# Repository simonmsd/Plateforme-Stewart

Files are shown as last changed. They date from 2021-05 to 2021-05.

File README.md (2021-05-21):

# Plateforme-Stewart
Réalisation d'une plateforme de stewart et  du tableur pour la contrôler.

Le document "Rapport_Projet.pdf" vous permet de découvrir notre travail et d'obtenir des informations sur comment nous avons réalisé le tableur et la plateforme.

Le document "Tableur_Stewart.xlsx" vous permet de déterminer les longueurs à donner aux bielles reliant les deux plateaux. Pour ce faire, il faut initialiser les paramètres des la plateforme dans les cellules "B1" à "B4". Ensuite, il faut entrer la position cible de la plateforme dans la colonne nommée "Cible" qui est la colonne "X", utiliser la fonction solveur d'Excel et lire les longueurs à donner aux bielles dans la colonne nommée "Longueurs ajustées" qui est la colonne "R".    

Dans le document "Vidéo de démonstration", vous trouverez un lien permettant d'accéder à une vidéo du foctionnement du tableur et de la plateforme de Stewart.

Le document "Rapport Projet.tex" est le code Latex qui a permis de créer le document pdf.

Dans le dossier "modélisations", vous trouverez les modélisations des deux plateaux de la plateforme de Stewart. Ces modélisations ont été réalisées avec le logiciel FreeCAD.

Dans le dossier "images", vous trouverez toutes les illustrations inclues dans le rapport du projet.

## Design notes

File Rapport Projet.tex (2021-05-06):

\documentclass[a4paper,12pt]{article}

% passe en mode large sur la page A4
\usepackage{a4wide}

% document francisé
\usepackage[french]{babel}

% permet la frappe de caractères accentués
\usepackage[utf8x]{inputenc}

\usepackage{bookmark}
\usepackage[T1]{fontenc}
\usepackage{color}
\usepackage{amsmath}
\usepackage{amsfonts}
\usepackage[top=3cm, bottom=3cm, left=2.5cm, right=2.5cm]{geometry}
\usepackage{fancyhdr}
\usepackage{graphicx}
\usepackage{float}
\usepackage{multicol}
\usepackage{multirow}
\usepackage{textcomp}
\usepackage{gensymb}
\usepackage{subcaption}
\usepackage{url}
\usepackage{hyperref}
\usepackage[justification=centering]{caption}

\pagestyle{fancy}

\makeatletter
\newcounter{subsubsubsection}[subsubsection]
\renewcommand\thesubsubsubsection{\@roman\c@subsubsubsection}
\newcommand\subsubsubsection{\@startsection{subsubsubsection}{4}{\z@}%
                                     {-3.25ex\@plus -1ex \@minus -.2ex}%
                                     {1.5ex \@plus .2ex}%
                                     {\normalfont\small\bfseries}}
\newcommand*\l@subsubsubsection{\@dottedtocline{3}{5.2em}{1em}}
\newcommand*{\subsubsubsectionmark}[1]{}
\setcounter{secnumdepth}{4}
\makeatother

% individualisation des paramètres de la page
%\parskip7pt
\setlength{\topmargin}{-10mm}
%\setlength{\textheight}{250mm}

%En-tête
\renewcommand{\headrulewidth}{0.3pt}
\fancyhead[C]{}
\fancyhead[L]{L1 CMI OPT/IM -- ICM -- INA}
\fancyhead[R]{Projet d'initiation à l'ingénierie}
\setlength{\headheight}{15pt}
%Pied de page
\renewcommand{\footrulewidth}{0.3pt}
\fancyfoot[L]{2020-2021}
\fancyfoot[C]{\textbf\small{\thepage}}
\fancyfoot[R]{\footnotesize{Rapport final}}

\begin{document}

%
% -------------------------------------------------------------------------------------------
%
\begin{figure}[H]
  \centering
  
\end{figure}

\begin{center}
	{\large {L1 CMI -- Projet d'initiation à l'ingénierie}} \\
	\vspace{6cm}
  {\Large \textbf{Conception et réalisation de la plateforme de Stewart} \\
	\vspace{2mm}
	Etudiants : Baptiste Deshayes, Malo Le Bourlout, Simon Massonnaud, Eliott Petiteau

    Encadrants : Rabah Bouzidi et  Nicolas Dupont-Bloch\\
	\vspace{9cm}	
	Janvier - mai 2021} \\
	\vspace{3mm}
	
\end{center}

\newpage

\tableofcontents

\newpage
%
% ====================================================================
%
\section{Introduction}

La plateforme de Stewart est un positionneur hexapode composé d’un plateau fixe et d’un plateau mobile. 
Ces deux plateaux sont maintenus à l’aide de six actionneurs linéaires qui s’apparentent à des vérins \textit{(nous les nommerons indifféremment aussi dans le rapport bielles ou tendeurs)}. Le but de cette plateforme est de s'adapter à tous les mouvements possibles.
Le plateau supérieur peut se déplacer selon les trois axes (x, y et z), il peut également s’incliner suivant trois axes. 
Grâce à ces six bielles pouvant indépendamment changer de longueur, la plateforme supérieure peut former n’importe quel plan, elle est juste limitée par la longueur des bielles. 
Il faut actionner les six bielles qui relient les deux plateaux pour faire varier leur longueur et ainsi changer l’orientation de la plateforme. 
Chaque position de la plateforme supérieure correspond à une seule combinaison des six longueurs.

\begin{figure}[H]
  \centering
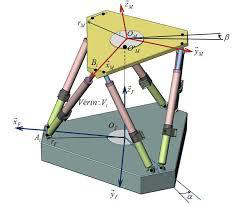
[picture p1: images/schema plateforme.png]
  
  \caption{Illustration de la plateforme de Stewart}
\end{figure}

\medskip

Cette plateforme peut avoir de nombreux usages. 
Elle peut être utilisée comme base pour une cabine de simulateur de vols, pour la conception de grues, la recherche
sous-marine ou encore pour les télescopes. 
Effectivement, la nature de ces activités nécessite un positionnement très précis et la plateforme de
Stewart répond à ce besoin. 
D’un coté, cette plateforme est une avancée technologique dans de nombreux secteurs car elle joue le rôle de simulateur. Elle permet donc d’anticiper des comportements sans avoir à réaliser des
tests en conditions réelles. Et d’un autre coté, cette plateforme a permis une excellente précision par rapport à ce qu'il était possible de réaliser auparavant.

\medskip

Notre projet a pour but d’équiper un télescope de Newton. 
Le principe de ce télescope est assez simple, en forme de tube. 
Les rayons lumineux rentrent à une extrémité du tube et sont projetés sur un miroir concave afin de diriger les rayons vers un autre miroir en face du premier. 
C’est ce deuxième miroir que nous regardons avec notre oeil sur le coté du tube ; ce miroir est incliné afin de changer la direction des rayons lumineux et de les faire parvenir à notre oeil. 
Pour avoir l’image la plus nette possible, il faut limiter le nombre de miroirs. 
Nous pouvons donc imaginer un télescope ayant juste le premier miroir et mettre notre oeil en face de ce dernier afin d’avoir une image la plus nette possible. 
Le problème est que notre tête va créer un zone d’obstruction trop importante. 
En effet, notre tête va éclipser une partie du ciel que nous voulons observer. 
Le but est donc de réduire au maximum cette zone d’obstruction. 
On utilise pour cela une caméra car elle est bien moins volumineuse que notre tête. 
On l’utilise également pour capter ces images et en prendre un cliché. 
Cette caméra nécessite d’être fixée au télescope et d’être à bonne distance du miroir. 
Il faut que la caméra soit à bonne distance afin d’être exactement sur le point focal, c’est la distance à laquelle tous les rayons réfléchis par le miroir concave se rejoignent et forment une image nette. 
Pour s’assurer que la caméra soit à la bonne distance, nous allons utiliser la plateforme de Stewart. 
Nous fixerons la caméra au centre du plateau supérieur et le plateau bas sera relié au télescope. 
Nous pourrons alors ajuster la position de la caméra très précisément afin d’être à la bonne distance focale. 

\begin{figure}[H]
    \centering
    \begin{subfigure}[]{0.4\textwidth}
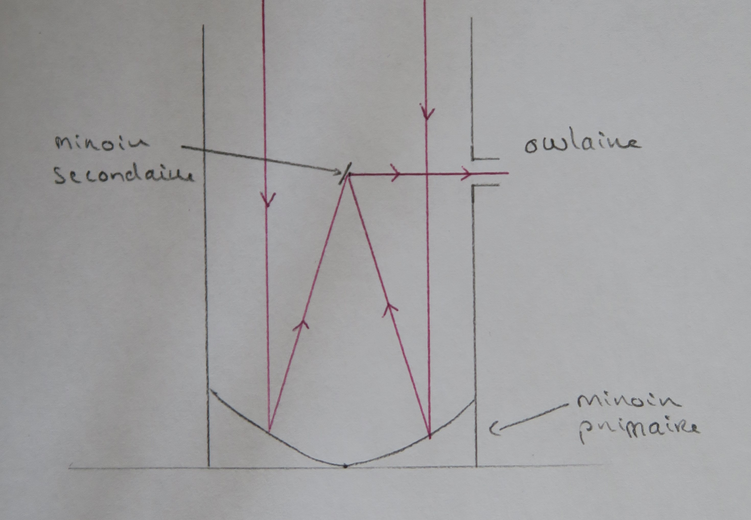
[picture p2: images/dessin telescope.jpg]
        
    \end{subfigure}
    \begin{subfigure}[]{0.4\textwidth}
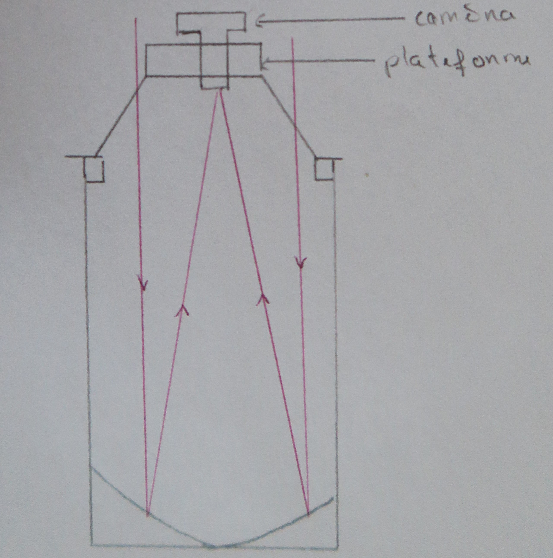
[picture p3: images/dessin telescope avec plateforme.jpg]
        
    \end{subfigure}
    \caption{Schéma du télescope de Newton avec et sans la plateforme de Stewart}
\end{figure}

\medskip

La temporalité du projet s'est séquencée en cinq temps : \\
-échanges/discussions avec notre encadrant sur les créneaux de cours pour guider l'avancement de notre projet ; \\
-échanges/discussions entre nous quatre pour mettre en commun et confronter nos temps de travail individuel, décider des options de conception et modélisation à prendre et de la marche à suivre pour engager les différentes étapes du projet ; \\
-temps de regroupement pour mettre en application ( = montage de la plateforme) ; \\
-finalisation de la réalisation de la plateforme ( = ajustements du montage) durant les vacances de printemps ; \\
-co-rédaction du rapport final.

\newpage

\section{Problématique}

Le problème traité dans ce projet est la réalisation d'une plateforme de Stewart qui se décompose en quatre étapes : \\
- la conception de celle-ci, en accord avec les dimensions requises pour sa future utilisation (ajuster la position d'une caméra sur un télescope de Newton), à l'aide d'un logiciel de modélisation 3D (ici FreeCAD) ; \\
- la création d'un tableur permettant de calculer et d'optimiser les longueurs des actionneurs linaires en fonction de la position voulue de la plateforme ; \\
- l'impression en 3D des pièces modélisées, l'achat des pièces de jonction et des actionneurs linéaires ; \\
- et enfin l'assemblage de la plateforme.

\medskip

Afin de créer une plateforme de Stewart, il nous est nécessaire de connaître  la cinématique de la plateforme et comment elle est affectée par les variations de longueur des six éléments linéaires qui la composent.
Il nous faut donc établir les différentes équations permettant de retrouver la longueur de chacun des éléments linéaires en fonction des mouvements de translation et de rotation que nous souhaitons effectuer. 

\medskip

La plateforme de Stewart est un outil dont l'utilisation est déjà répandue dans de multiples domaines, possédant donc diverses analyses sur son comportement, souvent abordées par cinématique inversée. 
Ses applications en robotique ont notamment fourni des analyses d'un point de vue électronique de la plateforme, ainsi que de sensibilité de ses mouvements dans le cadre de différents usages tel l'aéronautique.

\newpage

\section{Mise en oeuvre de la plateforme}

Dans cette partie, nous allons voir comment résoudre le problème posé. 
Cette résolution passe par deux grandes étapes.
Dans un premier temps, nous devons réaliser le modèle mathématique qui permet de contrôler la plateforme, nous avons pour cela créé un tableur Excel. Dans un second temps, nous devons créer la plateforme en elle-même, c'est-à-dire la modéliser pour qu'elle réponde à toutes les contraintes amenées par et pour sa future utilisation.

\subsection{Formulation cinématique}
	
L’objectif de ce tableur est de créer un modèle mathématique théorique et précis pour contrôler le fonctionnement de la plateforme de Stewart. 
Nous supposons, pour créer ce modèle, que la plateforme s’apparente à deux disques reliés par six axes et espacés d’une hauteur fixée quand l’appareil est au repos. 
Nous avons séparé notre travail en étudiant d’un côté, la partie basse de la plateforme et de l’autre, sa partie haute.

\subsubsection{Partie basse de la plateforme}

Intéressons-nous à la partie basse. 
Nous supposons que le disque qui la constitue est divisé en trois. C’est-à-dire que chaque point est séparé de cent vingt degrés en prenant des points aux angles 0\degree, 120\degree et 240\degree. 
Ensuite, nous fixons un écart par rapport à ces angles qui peut être choisi par l’utilisateur. 
Nous appelons cet écart \og delta thêta \fg. Il représente la position des six points d’accroches de nos axes. 
De chaque côté des trois angles principaux, de 0\degree, 120\degree et 240\degree, nous ajoutons la valeur de \og delta thêta \fg \ pour trouver un premier point et nous la retirons pour trouver un deuxième point. 
Prenons un exemple pour illustrer le fonctionnement de ce \og delta thêta \fg . 
Prenons-le de 30\degree et prenons le point à l’angle 0\degree. Comme expliqué, nous trouvons donc un point à 30\degree et un autre à -30\degree ou 330\degree. 
Une fois ces points déterminés, nous calculons leur valeur en radians. 
De ces valeurs en radians, nous pouvons déterminer les coordonnées des points selon les axes x, y et z. 
Pour la coordonnée selon l’axe z, elle vaut 0 car nous sommes sur la partie basse de la plateforme. 
Pour les coordonnées selon les axes x et y, nous appliquons respectivement la fonction cosinus et sinus à chaque angle tout en multipliant par le rayon de la plateforme. 
Nous connaissons donc les coordonnées des six points bas de la plateforme.

\begin{figure}[H]
  \centering
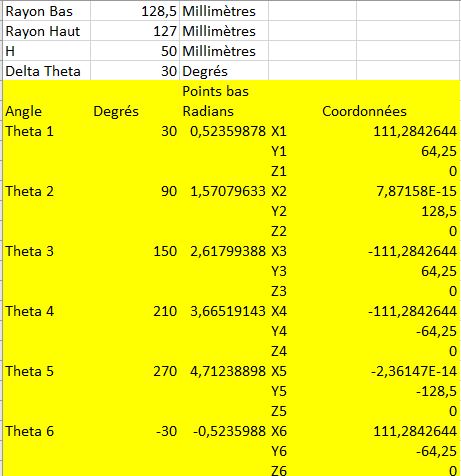
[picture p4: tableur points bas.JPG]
  
  \caption{Tableur points bas}
\end{figure}

\subsubsection{Partie haute de la plateforme}

Intéressons-nous maintenant à la partie haute de la plateforme. 
Nous supposons que ce disque est parfaitement parallèle à la partie basse et que ces deux disques sont séparés d’une hauteur fixée nommée \og h \fg . 
Nous supposons là aussi que le disque est séparé en trois points selon les mêmes positions que pour la partie basse de la plateforme. 
Ces trois points représentent les points d’arrivées des six axes qui partent de la partie basse. 
Nous calculons, suivant le même raisonnement que précédemment, les coordonnées de ces points selon les axes x, y et z, à une différence près. 
En effet, comme nous étudions maintenant la partie haute de la plateforme, nous nous trouvons à une hauteur \og h \fg \ de la partie basse. 
Ainsi la coordonnée selon l’axe z vaut h.  
Nous connaissons maintenant les coordonnées théoriques de chacun des trois points de la partie haute de la plateforme. 
Ces coordonnées théoriques seront modifiées par la suite lors de l’utilisation de la plateforme. 
Ces nouvelles coordonnées seront appelées \og coordonnées ajustées \fg . 
Au début, nous initialisons ces coordonnées ajustées avec les coordonnées théoriques pour continuer de réaliser le modèle mathématique.  
Nous calculons ensuite les écarts entre les points AB, AC et BC selon les axes x, y et z. 
Pour cela, nous calculons la différence entre les coordonnées. 
Ensuite, à partir de ces distances entre tous les points, nous pouvons calculer la norme des trois vecteurs que sont $\overrightarrow{AB}$, $\overrightarrow{AC}$, et $\overrightarrow{BC}$. Nous définissons également une valeur cible pour la norme des vecteurs. 
Cette valeur vaut racine de trois multipliée par le rayon de la plateforme haute. 

\begin{figure}[H]
  \centering
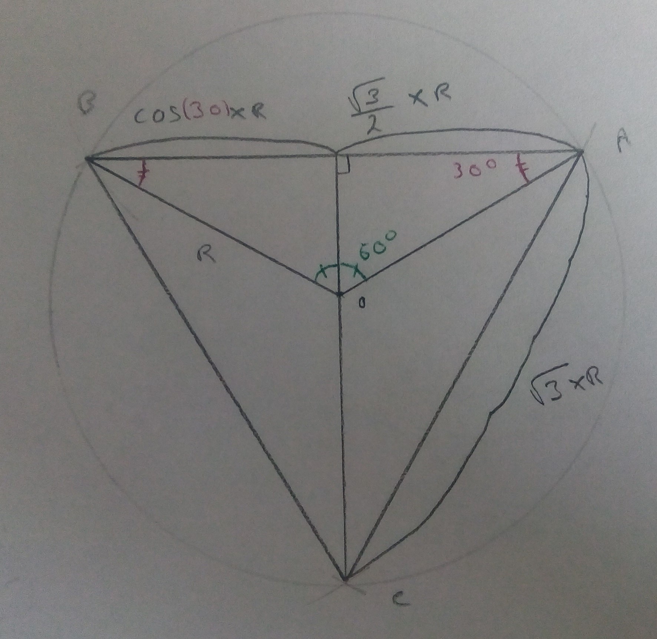
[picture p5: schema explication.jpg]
  
  \caption{Schéma d'explication pour le calcul de la norme des vecteurs}
\end{figure}

Nous calculons ensuite le produit vectoriel de $\overrightarrow{AB}$ par $\overrightarrow{AC}$ ainsi que sa norme car ce calcul va intervenir plus tard dans le tableur. 
Nous créons également une colonne qui contiendra les coordonnées ajustées des points hauts, mais nous y reviendrons plus tard. En effet, cette colonne n'intervient qu'à la toute fin du tableur.

\begin{figure}[H]
  \centering
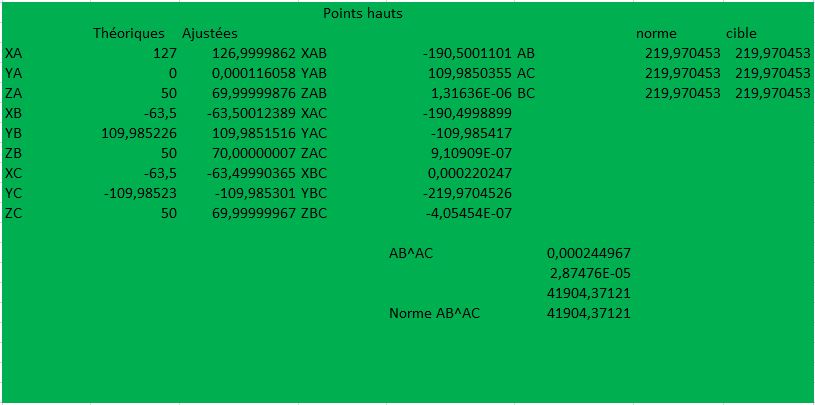
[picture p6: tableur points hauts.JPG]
  
  \caption{Tableur points hauts}
\end{figure}

\subsubsection{Longueurs des bielles qui relient les plateaux}

Maintenant que nous connaissons les coordonnées de tous les points d'accroches, nous pouvons raisonner sur la longueur des bielles, ce qui est l'objectif principal, c'est-à-dire déterminer leurs longueurs en fonction de la position voulue. 
Pour chacune des bielles, nous calculons sa longueur à partir des coordonnées théoriques de chaque point. 
Nous calculons la différence entre la coordonnée du point haut et celle du point bas selon chaque axe. 
Nous élevons ces différences au carré puis nous ajoutons les valeurs pour chaque axe et nous en prenons la racine carrée afin de connaître la longueur de la bielle. 
Étant donné que nous avons six bielles, nous répétons l'opération pour chacune d'elles. 
Dans cette partie du tableur, nous créons une colonne appelée \og longueurs ajustées \fg . 
C'est dans celle-ci que nous pourrons lire la valeur de la longueur qu'il faudra donner à chaque bielle pour pouvoir placer la plateforme à la position voulue. 
Nous créons, pour clôturer cette partie du tableur, une dernière colonne dans laquelle nous pouvons lire l'écart de longueur delta entre les bielles à l'origine et la longueur de chaque bielle pour la position voulue.

\begin{figure}[H]
  \centering
  
  \caption{Tableur bielles}
\end{figure}

\subsubsection{Valeurs cibles à obtenir}

Voyons maintenant la dernière partie du modèle mathématique, celle qui nous permet de donner la position souhaitée de la plateforme et qui permet de déterminer la longueur à donner aux bielles. Pour commencer, nous déterminons la position du point au centre du plateau haut. 
Nous appelons ce point \og G \fg. 
La coordonnée en x de ce point est la moyenne des coordonnées ajustées des points hauts selon cet axe. 
Nous suivons la même procédure pour chacun des axes. 
Nous créons ensuite une partie dédiée au centre de masse de la plateforme haute. 
Pour déterminer la valeur selon x de ce centre de masse, nous effectuons simplement la division de la coordonnée en x du produit vectoriel de $\overrightarrow{AB}$ par $\overrightarrow{AC}$ par sa norme. 
Nous répétons le même calcul pour les deux autres axes. 
Ensuite, nous créons une colonne où nous entrons les valeurs \og cibles \fg. 
Ces valeurs correspondent à la position que nous voulons donner au point qui est au centre de la plateforme, le point G. 
Nous pouvons également donner une valeur cible aux coordonnées en x et y du centre de masse. Ensuite, nous calculons les écarts entre la valeur cible et la valeur théorique des coordonnées du point G et du centre de masse. 
Nous élevons ces écarts au carré pour n'avoir que des valeurs positives. 
Nous sommons ensuite tous ces écarts, ce sera notre fonction \og coût \fg. 
Nous faisons également le choix de pouvoir donner des coefficients à ces valeurs pour agir plus ou moins sur le centre de masse ou les coordonnées du point G.

\begin{figure}[H]
  \centering
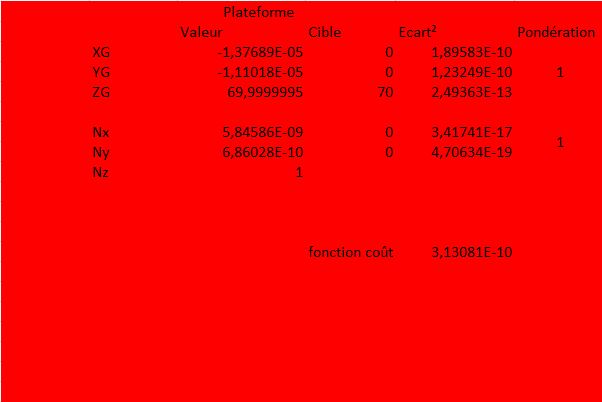
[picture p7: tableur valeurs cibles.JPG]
  
  \caption{Tableur valeurs cibles}
\end{figure}

\subsubsection{Fonction solveur}

Maintenant nous allons expliquer comment nous obtenons les longueurs ajustées des bielles. 
Nous utilisons pour cela la fonction solveur du tableur Excel. 
Le but est de minimiser la fonction coût, qu'elle soit la plus proche possible de zéro. 
Nous avons également une contrainte : il faut que les normes des vecteurs $\overrightarrow{AB}$, $\overrightarrow{AC}$, et $\overrightarrow{BC}$ soient égales ou du moins les plus proches possibles des normes cibles de ces vecteurs. 
Nos variables sont les coordonnées ajustées des points hauts. 
En les modifiant, nous calculons les longueurs ajustées des bielles qui sont donc les longueurs finales à donner aux bielles pour avoir la plateforme à la position souhaitée. 
En appliquant donc la fonction solveur, nous pouvons pour chaque position souhaitée obtenir la longueur à donner aux bielles.

\begin{figure}[H]
  \centering
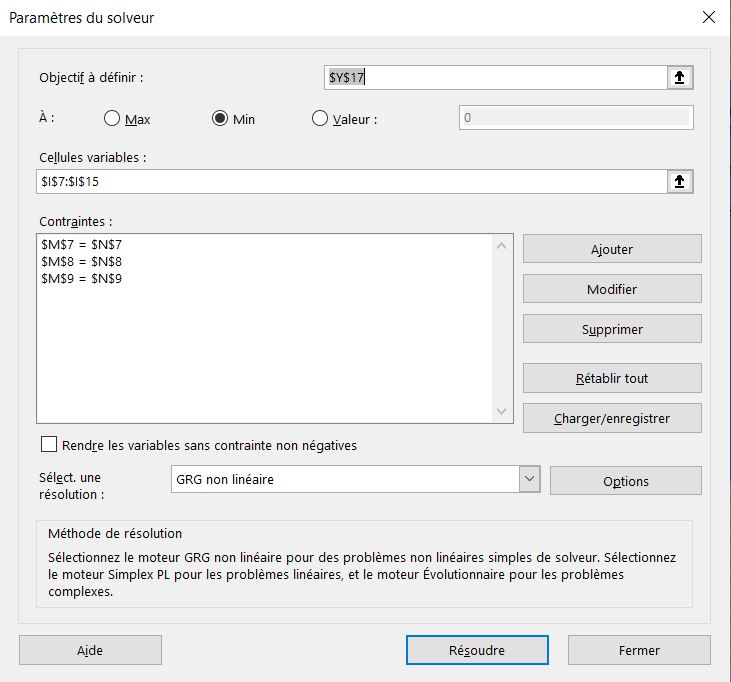
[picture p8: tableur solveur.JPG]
  
  \caption{Tableur solveur}
\end{figure}

\subsection{Réalisation de la plateforme}
La plateforme est composée de deux plateaux, un plateau inférieur et un plateau supérieur. 
Les attentes de ces deux plateaux sont différentes donc leur apparence et leur modélisation le seront aussi.

\subsubsection{Contraintes de la plateforme}

\subsubsubsection{Plateau inférieur}

Le plateau inférieur a quelques contraintes,
notamment cette première : obstruer le moins possible le passage de la lumière qui doit arriver jusqu’au télescope. 
Pour cela nous décidons de l'évider (ne modéliser que les bords extérieurs du cercle). 
Le plateau doit aussi s’emboîter parfaitement dans le tube du télescope sans bouger et ainsi garder l’ensemble de la plateforme stable. 
Nous décidons donc de créer une bordure de quelques millimètres, ainsi une partie s’imbriquera parfaitement dans le télescope et l’autre sera trop grande empêchant la plateforme de rentrer entièrement. 
Enfin, nous devons modéliser six trous à intervalles réguliers qui faciliteront le perçage après impression, intervalles choisis au préalable via les calculs mathématiques précédemment exposés et selon les besoins de la plateforme. 
Ces trous serviront plus tard à visser les tendeurs, il faut donc les modéliser en gardant bien cette idée à l’esprit. C’est pourquoi nous les modélisons sur la plus grande bordure (extérieure au tube du télescope) pour éviter une quelconque gêne des tendeurs à la pose ou à la stabilité de la plateforme dans le tube.

\begin{figure}[H]
  \centering
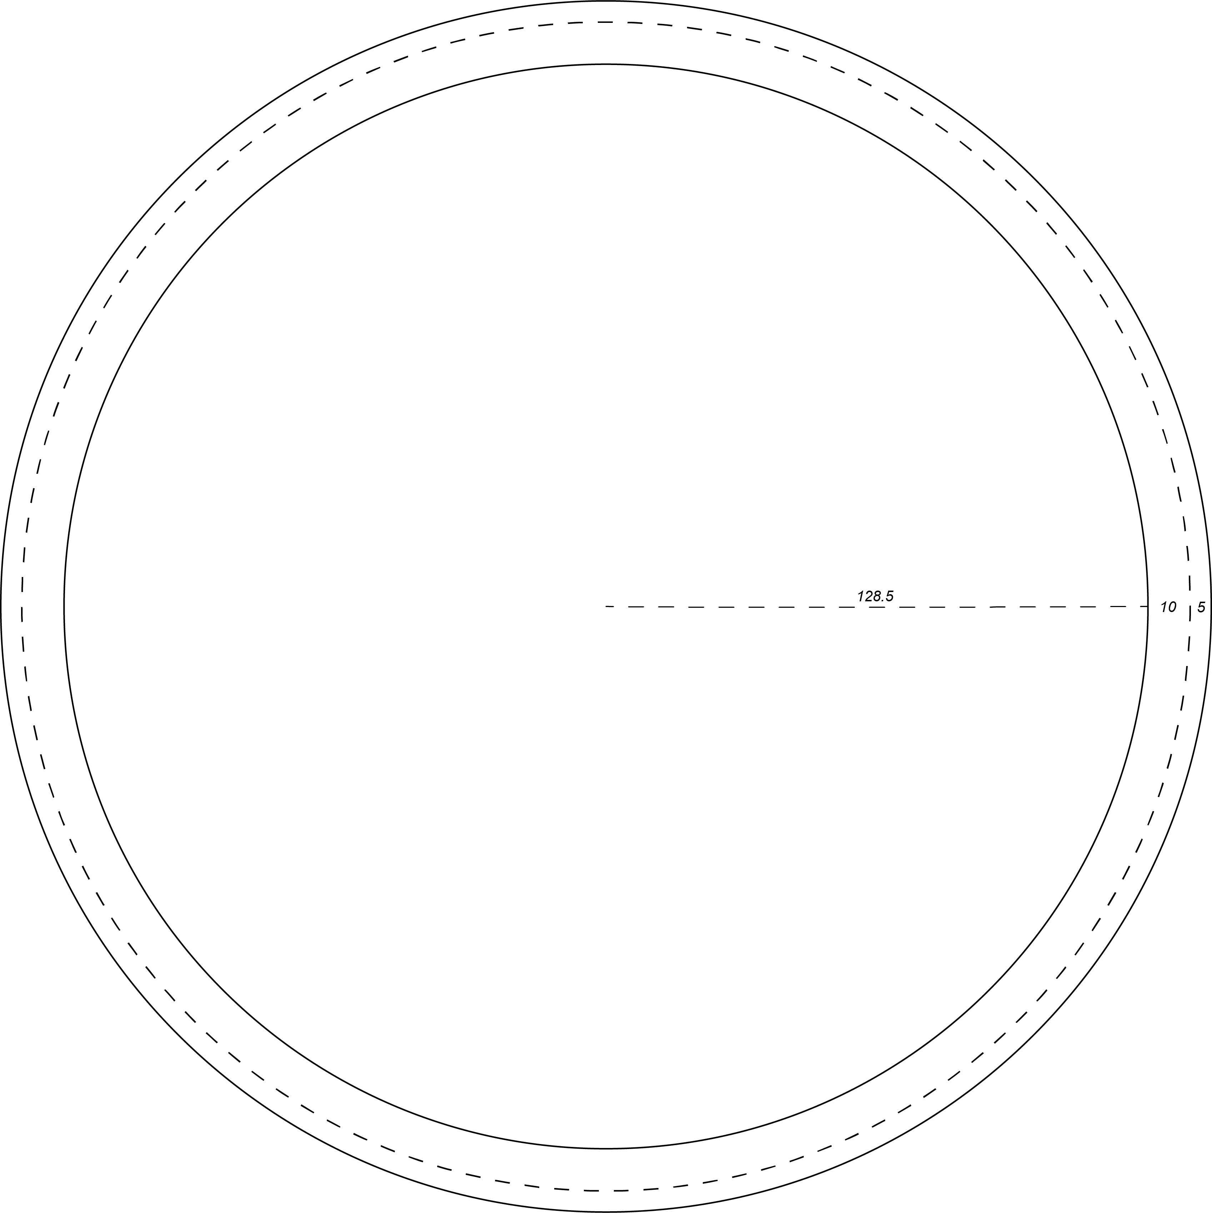
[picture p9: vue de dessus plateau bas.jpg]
  
  \caption{Vue de dessus plateau bas}
\end{figure}
\begin{figure}[H]
  \centering
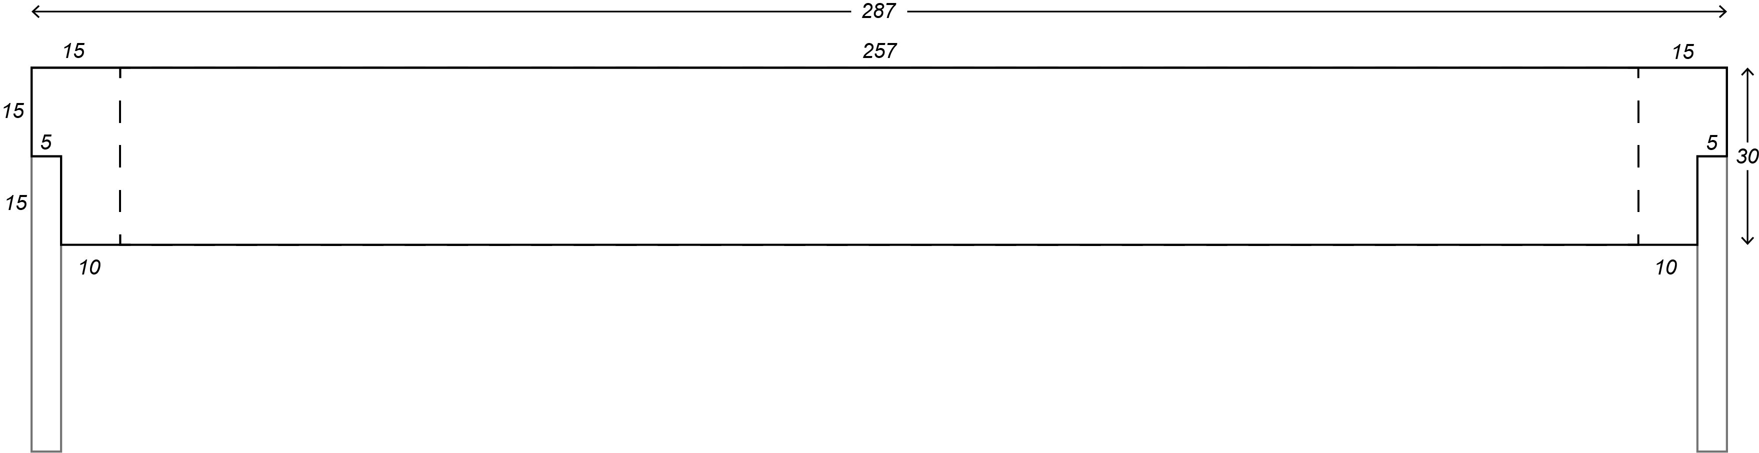
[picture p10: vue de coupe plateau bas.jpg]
  
  \caption{Vue de coupe plateau bas}
\end{figure}

\subsubsubsection{Plateau supérieur}

Pour le plateau supérieur, la première contrainte est la même : obstruer le moins possible le passage de la lumière.
Mais sachant que ce plateau doit porter en son centre une caméra, la tâche est plus compliquée que précédemment ; nous y reviendrons point par point.
Comme le plateau doit porter une caméra, il doit être en conséquence assez résistant, donc plus large.
Nous ne modélisons donc, sur le même principe que le plateau inférieur, que les bords extérieurs et laissons le centre évidé pour laisser passer la lumière.  
Il doit aussi contenir de la matière au centre  pour poser la caméra. Nous modélisons donc un rond central évidé où emboîter la caméra. 
La question d’obstruction de la lumière ne vient pas ici car la caméra étant posée dessus, elle obstruerait de toute façon la lumière.
Il nous faut maintenant relier le cercle central aux bordures car seulement les bordures seront portées par les tendeurs, nous le rappelons. 
Il faut modéliser des branches reliant les différentes parties du plateau. Mais pas trop en nombre ni trop larges pour ne pas obstruer la lumière. 
Nous modélisons donc trois branches, nombre raisonnable choisi arbitrairement, mais facilitant la modélisation par rapport aux six trous sur le plateau qui seront groupés par deux. 
Pour augmenter la résistance des branches sans obstruer davantage la lumière, nous les modélisons avec plus de matière dans le sens de la hauteur.
Mais si toute la plateforme est faite ainsi, il y aura un problème pour l’accès des tendeurs entre les deux plateformes avec le surplus de matière les empêchant de bouger sans contrainte. 
Nous enlevons donc de la matière petit à petit à partir du centre, laissant ainsi une partie volumineuse et solide au niveau de la caméra et une partie plus fine en extérieur laissant plus libre champ aux tendeurs.

\begin{figure}[H]
  \centering
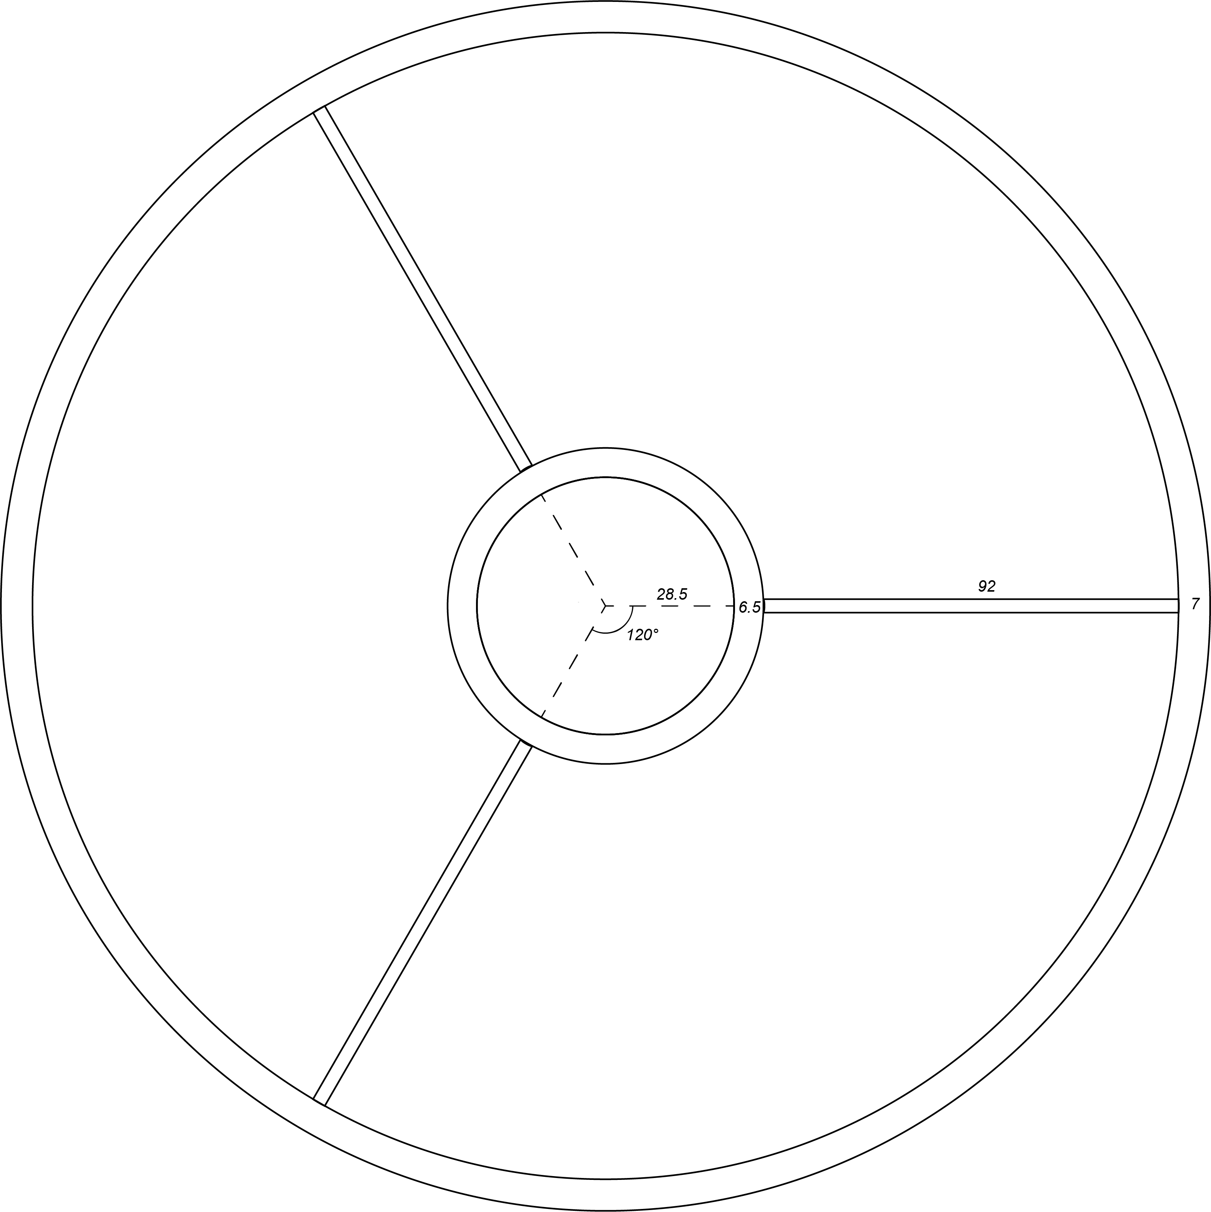
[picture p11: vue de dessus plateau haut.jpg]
  
  \caption{Vue de dessus plateau haut}
\end{figure}

\begin{figure}[H]
  \centering
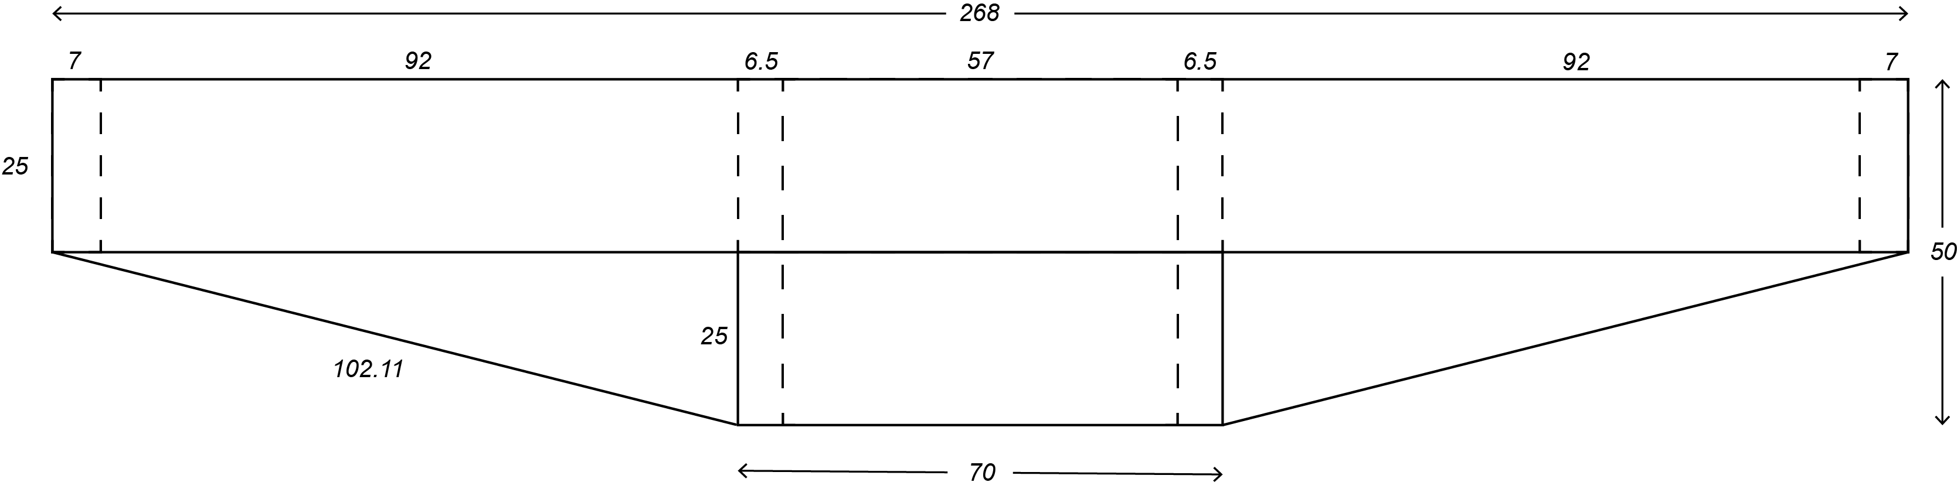
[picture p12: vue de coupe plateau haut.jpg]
  
  \caption{Vue de coupe plateau haut}
\end{figure}

\subsubsection{Modélisation de la plateforme}

\subsubsubsection{Plateau inférieur}

Modélisation du plateau inférieur :
modélisation avec le logiciel FreeCAD. Fonctionnement à partir de schéma 2D auquel nous rajoutons de la matière. Nous réalisons donc d’abord sur le schéma deux cercles différents avec les diamètres  aux bordures afin d’y ajouter plus ou moins de matière et créer la bordure nécessaire.

\begin{figure}[H]
    \centering
    \begin{subfigure}[]{0.4\textwidth}
        
    \end{subfigure}
    \begin{subfigure}[]{0.4\textwidth}
        
    \end{subfigure}
    \caption{Schéma et modélisation du plateau bas}
\end{figure}

Pour finir, il nous faut modéliser des petits trous afin de faciliter le perçage après impression.
Pour enlever la matière, même principe que pour en créer : d’abord, faire un schéma 2D du trou recherché puis enlever la matière en fonction de ce schéma. 
Pour éviter de faire six schémas pour chacun des six trous, il existe une fonctionnalité sur FreeCAD qui répète une action de façon circulaire. Donc, une fois le premier trou modélisé, il suffit de rentrer le nombre de trous souhaités et ils sont repartis de façon régulière autour de l’axe choisi.

\begin{figure}[H]
    \centering
    \begin{subfigure}[]{0.4\textwidth}
        
    \end{subfigure}
    \begin{subfigure}[]{0.4\textwidth}
        
    \end{subfigure}
    \caption{Schéma et modélisation des trous du plateau bas}
\end{figure}

\subsubsubsection{Plateau supérieur}

Même principe pour le plateau supérieur. D’abord, effectuer le schéma avant d’ajouter ou de retirer la matière.
Nous commençons donc par dessiner et modéliser juste une partie du plateau pour une question de précision lors du placement des branches. Puis, nous modélisons les trous au bout de la branche présente à l’aide toujours de schéma.

\begin{figure}[H]
    \centering
    \begin{subfigure}[]{0.25\textwidth}
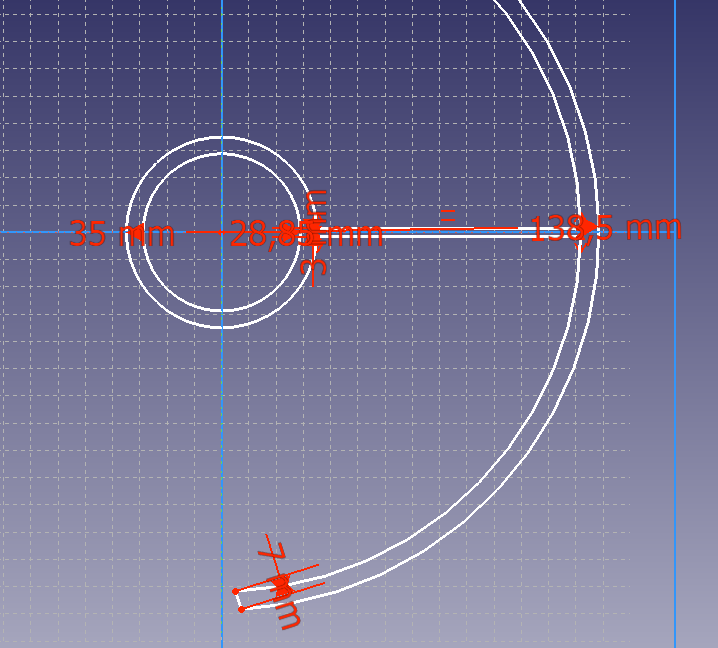
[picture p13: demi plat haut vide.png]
        
    \end{subfigure}
    \begin{subfigure}[]{0.3\textwidth}
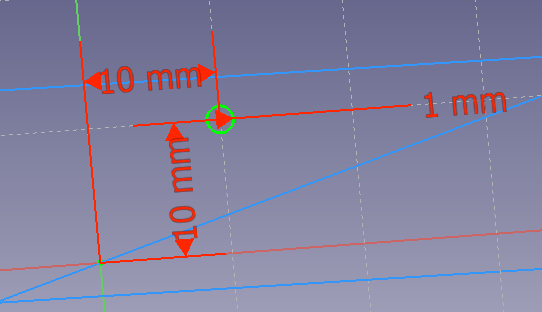
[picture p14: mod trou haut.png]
        
    \end{subfigure}
    \begin{subfigure}[]{0.3\textwidth}
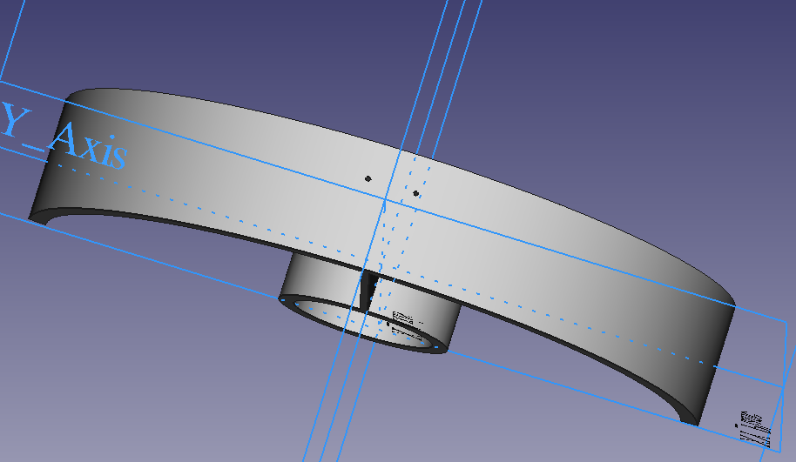
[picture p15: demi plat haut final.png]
        
    \end{subfigure}
    \caption{Schéma et modélisation du plateau et des trous du plateau haut}
\end{figure}

Puis, nous réutilisons la fonctionnalité de répétition circulaire pour refaire le tout trois fois afin d’avoir les trous et les branches à intervalles réguliers. Sur cette action, nous constatons que certaines parties de matière se chevauchent, mais cela n’est qu’un détail car lors de l’impression cela ne changera rien. 

\begin{figure}[H]
    \centering
    
    \caption{Plateau haut après l'utilisation de la fonctionnalité de répétition circulaire}
\end{figure}

Enfin, pour faciliter l’accès des tendeurs entre les deux plateaux, nous décidons de rogner de façon triangulaire les branches et l’anneau extérieur. Pour ce faire, toujours le même procédé : d’abord réaliser un schéma représentant la forme à rogner puis utiliser la fonctionnalité de déblaiement circulaire tout autour de l’axe central.

\begin{figure}[H]
    \centering
    \begin{subfigure}[]{0.4\textwidth}
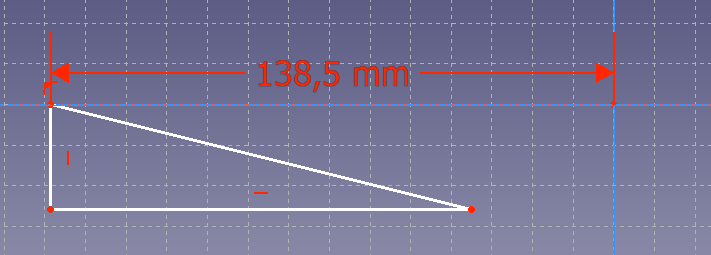
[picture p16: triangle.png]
        
    \end{subfigure}
    \begin{subfigure}[]{0.3\textwidth}
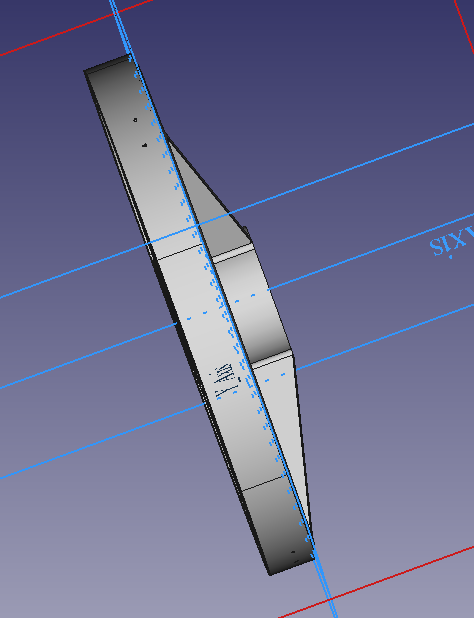
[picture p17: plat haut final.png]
        
    \end{subfigure}
    \caption{Schéma de la figure à rogner et plateau haut après rognage}
\end{figure}

\subsubsection{Impression de la plateforme}

Une fois toutes ces étapes réalisées, nous avons exporté les deux modélisations en fichier \og .stl \fg, fichier que l’imprimante est capable de lire. 
Puis, nous les avons mis sur clé et les avons connectés à l’imprimante pour impression.

\newpage

\section{Expérimentation}

Une fois les pièces imprimées et les bielles reçues, nous sommes passés à la construction de la plateforme. 
Là, un problème est apparu dès le démarrage. 
Les trous du plateau bas sont trop espacés pour qu'il y ait un espace suffisant entre les deux plateaux. 
Pour satisfaire à la résolution de ce problème, nous décidons de réduire l'espace entre ceux-ci à quatre-vingt-quinze millimètres -c'est la distance trou à trou en ligne droite-, cela nous permettant d'obtenir une hauteur entre les deux plateaux de cinquante millimètres. 
Nous perçons des trous de trois millimètres de diamètre pour y insérer vis et écrous et ainsi assurer une bonne fixation. De plus, nous plaçons des rondelles de part et d'autre des rotules afin que celles-ci puissent avoir un mouvement libre et nous plaçons également des rondelles avant les écrous pour éviter que cela n’endommage les plateaux qui sont en acide polylactique (PLA), une matière plastique d’origine végétale, utilisée en impression 3D. 

\begin{figure}[H]
  \centering
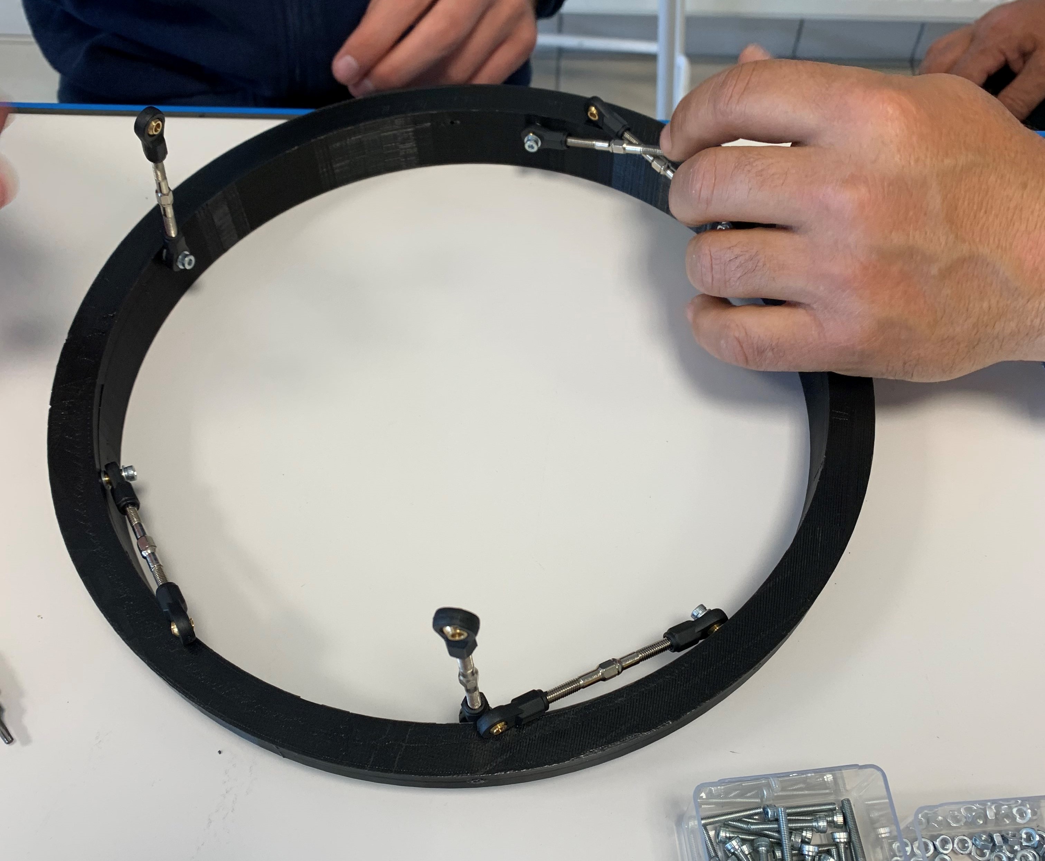
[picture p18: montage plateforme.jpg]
  
  \caption{Montage de la plateforme}
\end{figure}

La deuxième étape consiste à mettre la plateforme à niveau.
Cependant, un problème est apparu ici. En effet, il y a une translation horizontale qui s'est créée entre les deux plateaux. Leurs centres ne sont plus alignés par une droite normale au plateau bas.
Ce problème vient du fait que, lors de l'impression, nous avions paramétré un espacement régulier des trous de fixations.
Toutefois, pour s'adapter aux contraintes venant des bielles, nous modifions l'espacement de ceux-ci  pour pouvoir réaliser le montage de la plateforme. 
En perçant donc de nouveaux trous dans le plateau bas pour remédier au problème de longueur des bielles, nous commettons des erreurs expérimentales et cela crée une sorte de déséquilibre de la plateforme. Les deux centres des plateaux ne sont donc plus parfaitement alignés, cependant nous réussissons à ce que les plateaux soient parallèles, ce qui est très important pour le fonctionnement sur le télescope. 
En effet, si les deux plateaux ne sont pas parallèles, il est impossible de prendre un cliché net avec la caméra placée sur le plateau haut. 
Cette translation montre aussi un autre aspect positif du montage, celui du déplacement du plateau qui se contrôle grâce à la longueur des bielles. 
En observant les longueurs des six bielles, nous remarquons que la position parallèle obtenue ne vient pas du fait que celles-ci sont les mêmes. C'est ce que nous avions fait au début. Nous avions monté la plateforme en mettant les six bielles à la même longueur et cela créait une inclinaison du plateau haut par rapport au plateau bas. 

\begin{figure}[H]
    \centering
    \begin{subfigure}[]{0.4\textwidth}
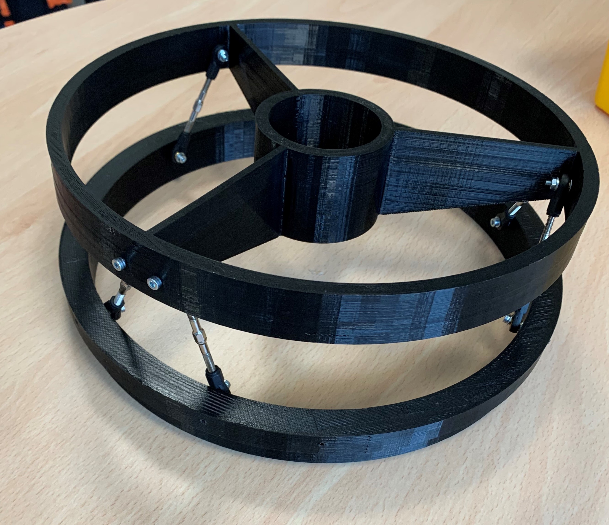
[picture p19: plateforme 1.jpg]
        
    \end{subfigure}
    \begin{subfigure}[]{0.5\textwidth}
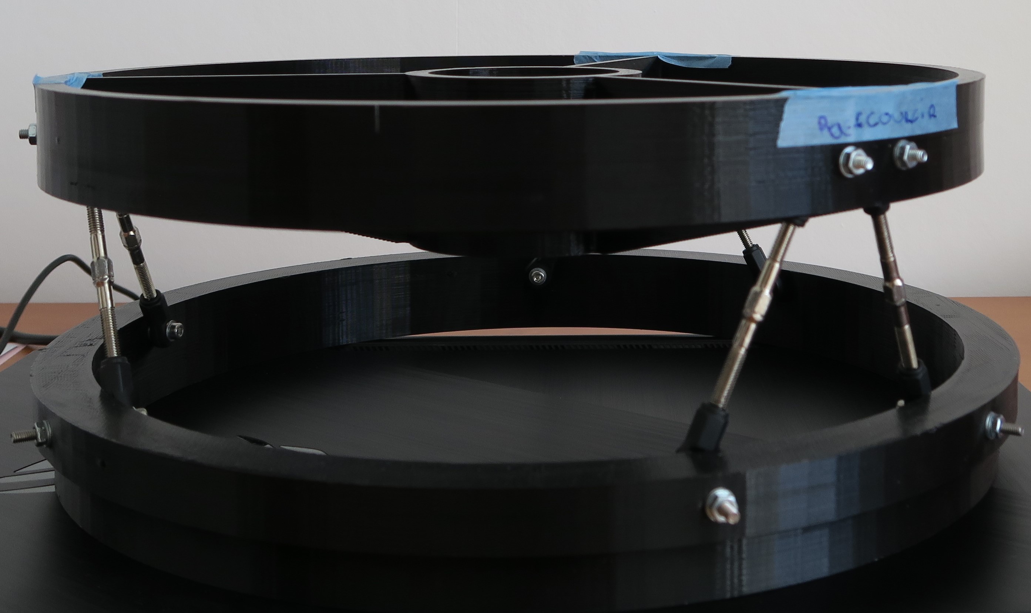
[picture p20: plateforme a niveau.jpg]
        
    \end{subfigure}
    \caption{Plateforme avant et après mise à niveau}
\end{figure}

Cela vient également en contradiction avec le tableur. En effet, le modèle théorique supposait que les six fixations des bielles sur le plateau bas étaient équidistantes. 
Cependant, le fait de repercer la plateforme pour répondre aux contraintes des bielles a faussé le tableur. 
Pour l'utilisation du modèle mathématique, nous avons donc mis une hauteur théorique, entre les deux plateaux, de cinquante millimètres et nous avons gardé un \og delta théta \fg \ de 30\degree.
Ces deux paramètres nous permettent néanmoins d'avoir un bon aperçu de l'utilisation du tableur.  

\begin{figure}[H]
  \centering
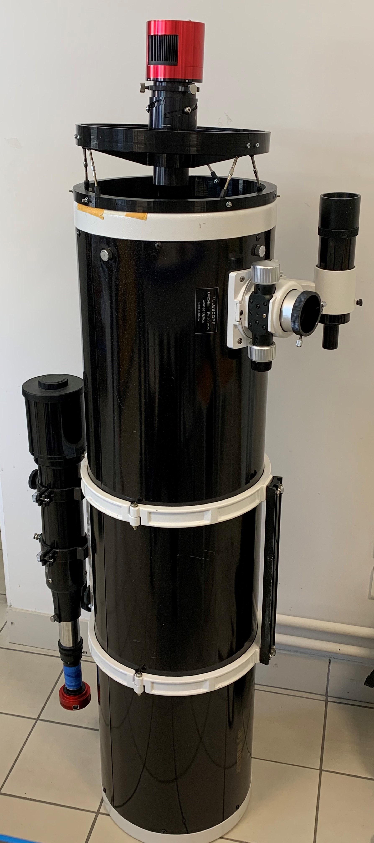
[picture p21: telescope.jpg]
  
  \caption{Montage de la plateforme sur le télescope}
\end{figure}

\newpage

\section{Conclusions et perspectives}

Ce projet, notre premier projet, nous permet de mieux appréhender
ce qu’est le métier d’ingénieur. La durée de ce projet ainsi que sa complexité nous donnent un premier aperçu de ce à quoi nous serons confrontés dans notre activité professionnelle. Cette
première approche nous initie aussi aux différentes étapes d’un projet. Nous avons
commencé par une phase conséquente de compréhension et de visualisation du fonctionnement de la plateforme de Stewart. Cette phase a été la plus
longue. Ensuite, nous avons recherché les formules mathématiques adéquates aux
mouvements de la plateforme, cette partie du projet est celle qui a été la plus compliquée
étant donné nos connaissances scientifiques et nos compétences techniques à ce stade de notre cursus. Néanmoins, grâce à de très nombreux échanges avec Monsieur Bouzidi, nous sommes parvenus à créer le tableur contrôlant les positions de la plateforme.  C'était une étape nécessaire et obligatoire avant d'aborder celles de la modélisation et de la réalisation.
Pour finir, la dernière étape était celle l’assemblage afin d’obtenir une plateforme opérationnelle.
Nous avons réussi à tenir les temps malgré des délais plus serrés sur la fin du projet,
toujours accompagnés de notre encadrant qui nous l'a bien exposé et ensuite bien guidé dans ses différentes étapes.
Ce projet nous aura aussi permis de travailler en collectif et de nous responsabiliser individuellement (temps collectifs de coordination d'équipe en présentiel et distanciel, répartition des tâches à réaliser (réflexion/conception/modélisation/application concrète), co-rédaction du rapport). 

\medskip

La plateforme est exactement aux bonnes dimensions pour recevoir le télescope et le
plateau supérieur aux bonnes dimensions pour accueillir la caméra. La plateforme est solide
et répond au besoin auquel nous faisons face. Cependant, les bielles sont
très dures à manoeuvrer pour en modifier la longueur. De plus, ces bielles sont trop courtes et ne permettent pas un espace suffisant entre les deux plateaux. Enfin, la translation entre les deux plateaux fait que la caméra ne se trouve pas exactement au niveau du point focal.

\medskip

Malgré tout, nous sommes allés jusqu'à la fin de la conception/réalisation de la plateforme de Stewart et le modèle est viable. La plateforme pourrait trouver une amélioration en l'équipant de nouveaux actionneurs linéaires plus à même de s'adapter aux contraintes d'utilisation et au modèle mathématique. Pour aller encore plus loin, il serait possible de créer un programme qui réglerait la plateforme automatiquement à la bonne distance, afin de disposer  d'une plateforme autonome. Il faudrait pour cela l'équiper de vérins contrôlés par des servomoteurs.
Il ne nous reste plus qu'à maintenant  tester le télescope équipé de sa plateforme pour ensuite admirer les clichés.

\begin{figure}[H]
  \centering
  
  \caption{Nébuleuse d'Orion (Nicolas Dupont-Bloch - \url{http://nicolas.dupontbloch.free.fr}
)}
\end{figure}

\newpage

\section{Remerciements}

Nous tenons à remercier notre encadrant, Monsieur Rabah Bouzidi, pour le temps qu'il nous a consacré tout au long du projet, ses explications, sa disponibilité et ses conseils. Nous le remercions également de bien avoir voulu imprimer la plateforme avec son équipement personnel, sans quoi le projet n'aurait pas abouti. 

\medskip

Nous remercions également Monsieur Cédric Doutriaux, responsable du FabLab, pour ses conseils, notamment quant à l'utilisation de FreeCAD, et sa disponibilité pour répondre à nos questions tout au long du projet.

\medskip

Pour finir, nous remercions Monsieur Nicolas Dupont-Bloch qui a été à l'origine de ce projet et qui nous a accordé le droit d'utiliser une de ses photos du ciel profond. (\url{http://nicolas.dupontbloch.free.fr})

\newpage
\section{Références}

Comme mentionné dans le rapport, ce projet a pris forme grâce aux très nombreux échanges que nous avons eu avec Monsieur Bouzidi, également ceux avec Monsieur Doutriaux. 
C'est pourquoi nous n'avons utilisé que peu de ressources externes. 
Voici toutefois les références utilisées durant le projet pour appréhender le fonctionnement de la plateforme de Stewart : 
\newline
-\url{https://www.xarg.org/paper/inverse-kinematics-of-a-stewart-platform/} 
\newline
-\url{http://www.scielo.br/scielo.php?script=sci_arttext&pid=S1678-58782012000200011}
\newline
-\url{https://www.3sigma.fr/Systemes_didactiques-Commande_de_la_plateforme_de_Stewart_Deltalab.html} 
\newline
-\url{https://fr.wikipedia.org/wiki/Plateforme_de_Stewart}

\bigskip

Voici le lien permettant d'accéder aux bielles que nous avons utilisées pour le montage de la pateforme :
\newline
\url{https://www.conrad.fr/p/barre-darticulation-reely-538057-1-pcs-1301679}

\bigskip

Voici l'accés au site internet de Monsieur Dupont-Bloch : 
\newline
\url{http://nicolas.dupontbloch.free.fr}

\bigskip

Vous trouverez tous nos documents sur le dépôt GitHub dont voici le lien :
\newline
\url{https://github.com/simonmsd/Plateforme-Stewart.git}

\bibliographystyle{plain}
\bibliography{CMIbib}

\end{document}

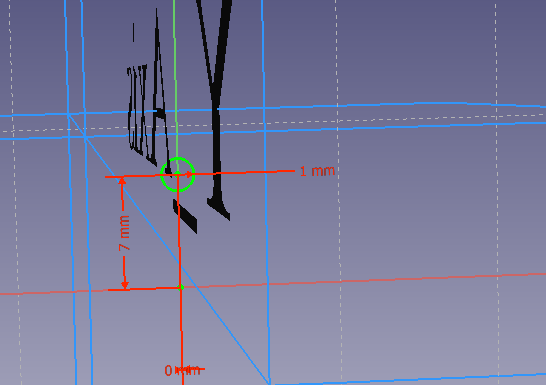
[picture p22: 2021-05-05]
images/plan trou.png

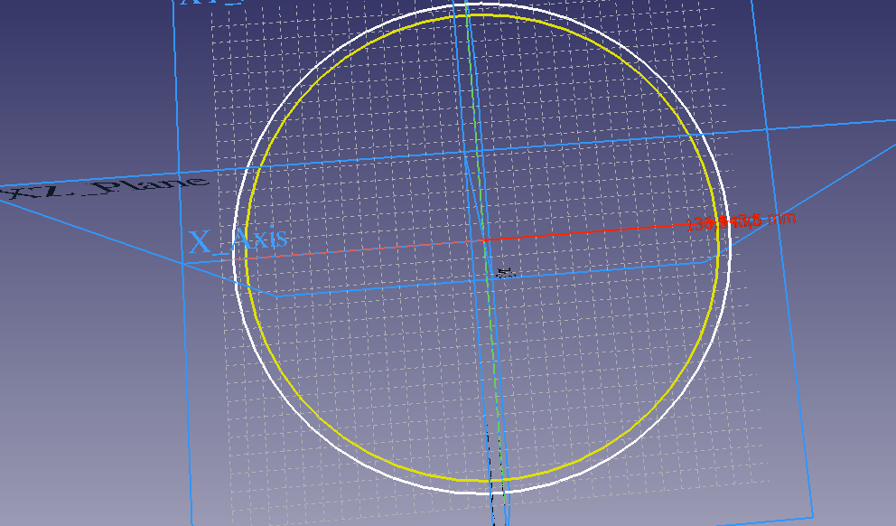
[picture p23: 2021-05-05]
images/mod plateau haut vide.png

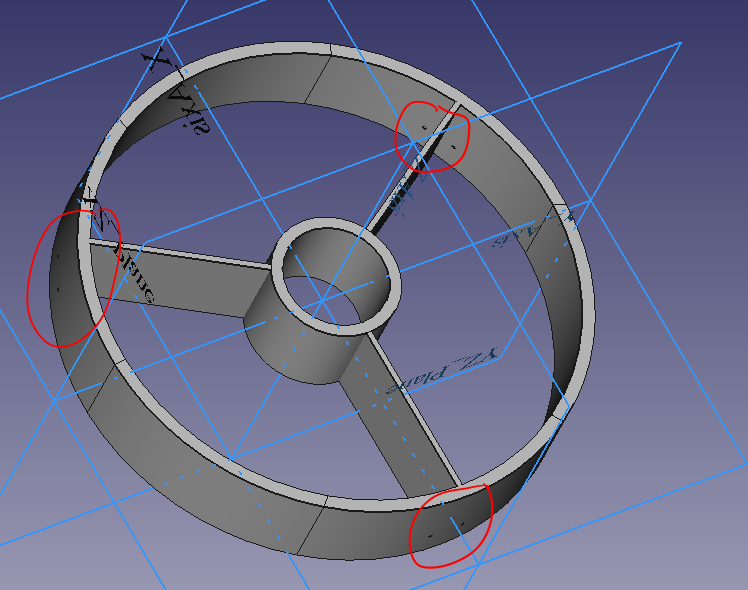
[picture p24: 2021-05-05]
images/plat hau trous.png

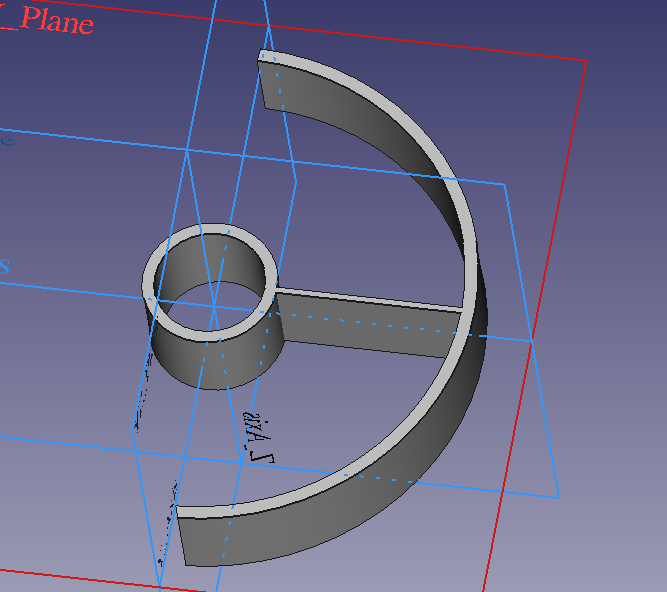
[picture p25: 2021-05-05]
images/demi plat haut plein.png

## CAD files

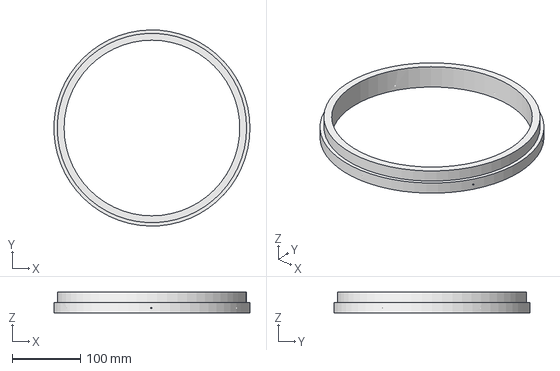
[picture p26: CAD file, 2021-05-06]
modélisations/Plateau bas.FCStd
286.8 x 287.0 x 30.0 mm

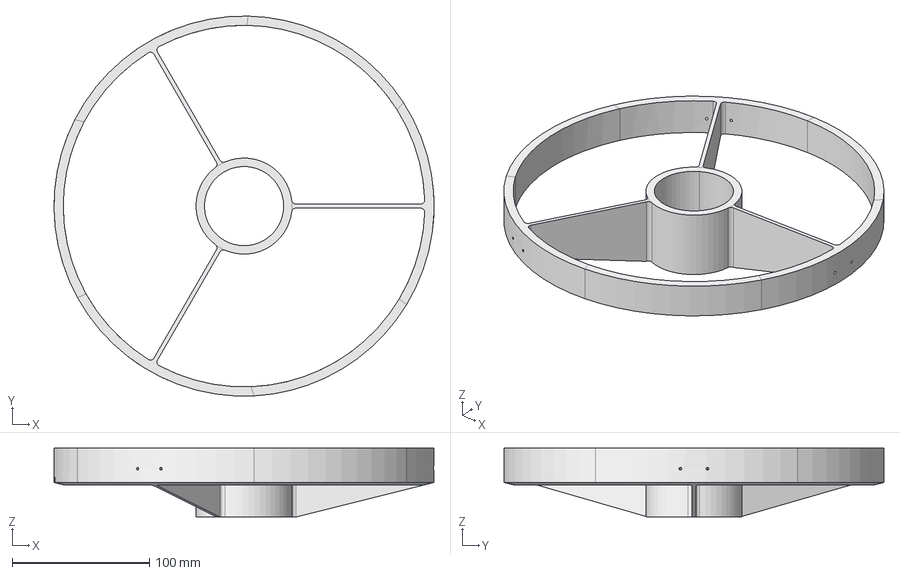
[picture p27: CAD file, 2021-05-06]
modélisations/Plateau camera.FCStd
276.9 x 276.8 x 50.0 mm

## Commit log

2021-05-05 Add files via upload
    Voici toutes les images et tous les schémas utilisés pour le rapport Latex
2021-05-21 Create Vidéo de démonstration
